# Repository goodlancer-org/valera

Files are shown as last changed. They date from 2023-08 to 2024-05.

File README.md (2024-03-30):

# Valera
Open source hardware and software social robot.






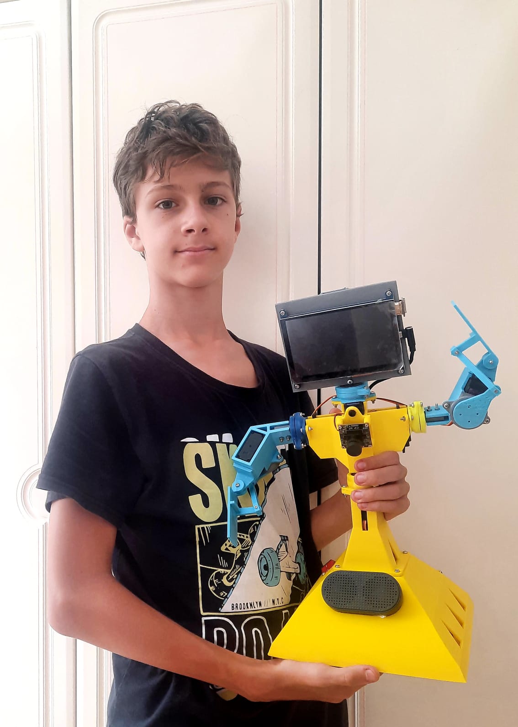
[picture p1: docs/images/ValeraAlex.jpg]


The goal behind the project is to make a social robot with AI on board as cheap and as easy to build and use as it possible.

The project is managed by GoodLancer team.

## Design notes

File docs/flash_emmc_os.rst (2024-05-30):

How to install Linux on eMMC
================================

Before we start
~~~~~~~~~~~~~~~~~

If you don't have a Linux installed on your eMMC you can install one manually.
You will need for this:

#. eMMC card to install Linux to 
#. eMMC-microSD adapter 
#. microSD-USB adapter to plug everything into the PC 
#. Software to flash the eMMC card, i.e. balenaEtcher

Step 1. Download Linux image
~~~~~~~~~~~~~~~

It's better to take an image from the microcomputer manufacturer website, in case of Orange Pi -
from http://www.orangepi.org/html/serviceAndSupport/index.html

3rd party distributions might be more feature rich or performant, but might be leaking some
drivers, i.e. i2c overlays, so in most cases it's safer to stay with Linux distributions 
provided by the microcomputer manufacturer.

In this example we will go with Ubuntu.

Step 2. Flash eMMC with Linux image
~~~~~~~~~~~~~~~

Step 3. Enable i2c in Linux settings
~~~~~~~~~~~~~~~

Use ``sudo orangepi-config`` to enable i2c on the computer how it's 
described on http://www.orangepi.org/orangepiwiki/index.php/Orange_Pi_3B#40pin_I2C_test_2

Step 4. Test if i2c is working
~~~~~~~~~~~~~~~

Check if i2c-2 is switched on by typing ``ls /dev/i2c-*``, you should see i2c-2 device in the list.
Type ``sudo i2cdetect -y 2`` to check if the device is accessible.

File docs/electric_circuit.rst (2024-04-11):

Electric Circuit
==================
On picture below you may see a block scheme depicting how Valera's electric curcuit is composed.
Please note that different versions of the robot uses different microcomputers.
Valera v0.1 utilises microcomputer ODROID-N2L whereas Valera v0.2 utilises Orange PI 3B.
Some images on this page are not updated to the new version of the robot, so if you
see 'Odroid' on the picture - it means any microcomputer, Odroid or Orange PI, otherwise
the difference should be stated in the text.

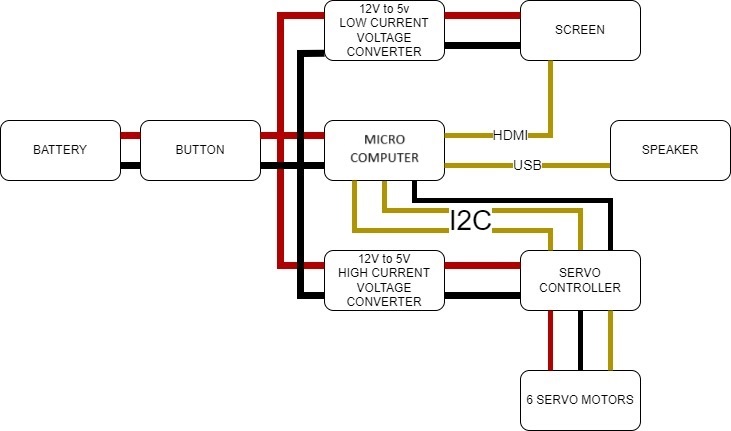
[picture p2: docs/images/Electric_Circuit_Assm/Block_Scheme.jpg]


|

That's how it looks in reality

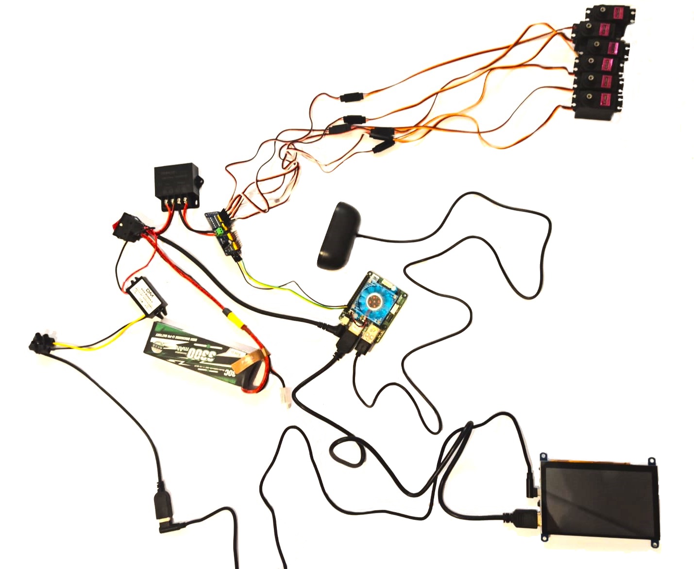
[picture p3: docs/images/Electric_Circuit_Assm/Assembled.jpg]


Assebling Instruction
---------------------

Before we start:
~~~~~~~~~~~~~~~~

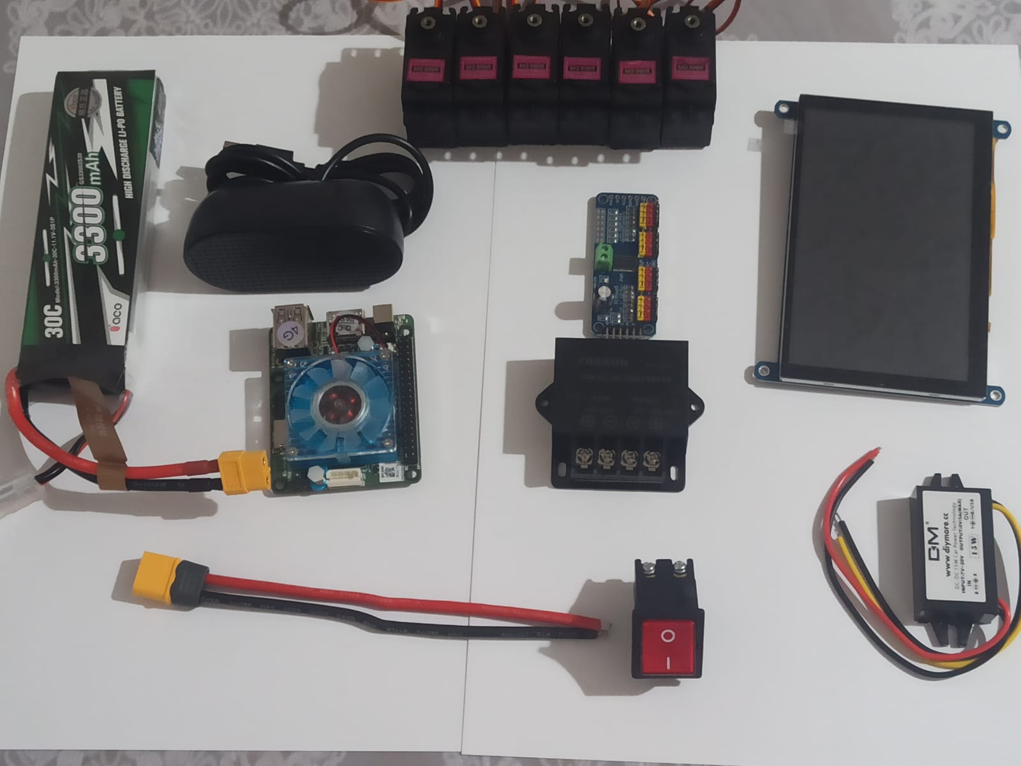
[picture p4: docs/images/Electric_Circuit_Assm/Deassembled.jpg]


Please watch the assembling process video or read a full instruction below.

|

.. raw:: html

    <iframe width="560" height="315" 
    src="https://www.youtube.com/embed/S_Jwx7noY1A?si=5r4jmpi5huq4Ma-H" 
    title="Assembly guide for the electrical circuit of the Valera robot" frameborder="0" 
    allow="accelerometer; autoplay; clipboard-write; encrypted-media; gyroscope; picture-in-picture; web-share" allowfullscreen>
    </iframe>

Step 1
~~~~~~~~~~
Connect low current voltage converter, two wires and jack cable
to the button form one side and XT60 wire from another side. Mind the polarity.

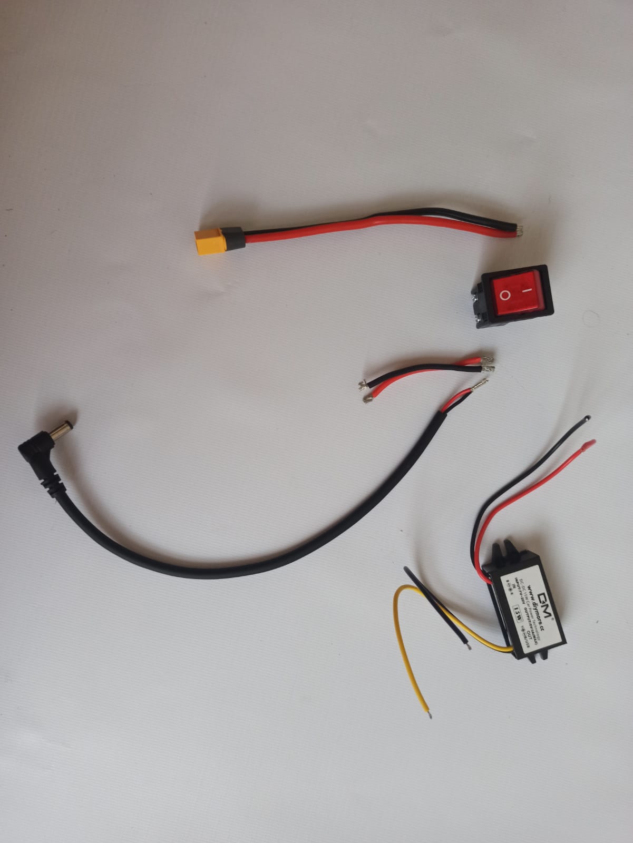
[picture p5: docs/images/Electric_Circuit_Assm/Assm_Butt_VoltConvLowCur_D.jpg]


|

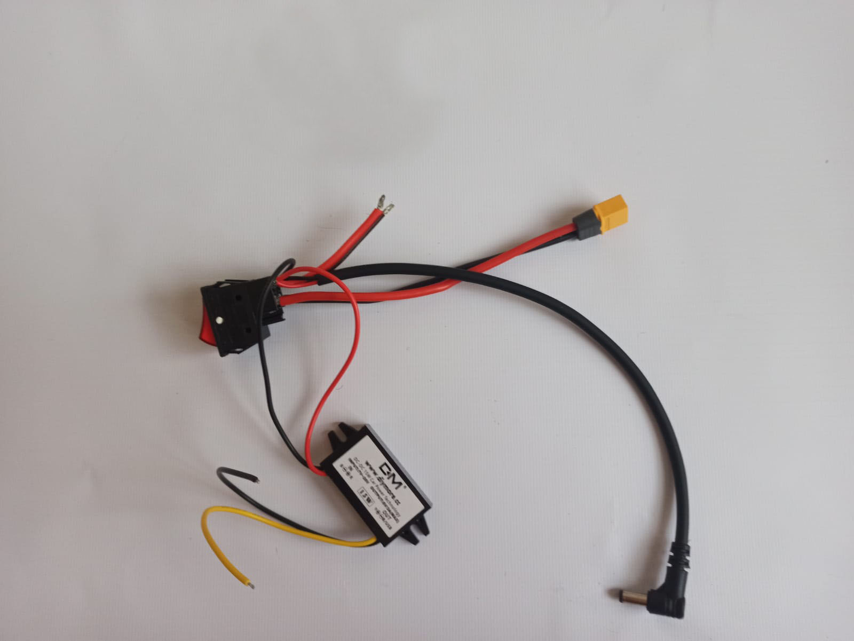
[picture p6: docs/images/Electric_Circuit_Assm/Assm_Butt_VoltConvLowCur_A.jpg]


Step 2
~~~~~~~~~~
Connect an input of the high current voltage converter to the two wires
we connected to the button before. Mind the polarity.

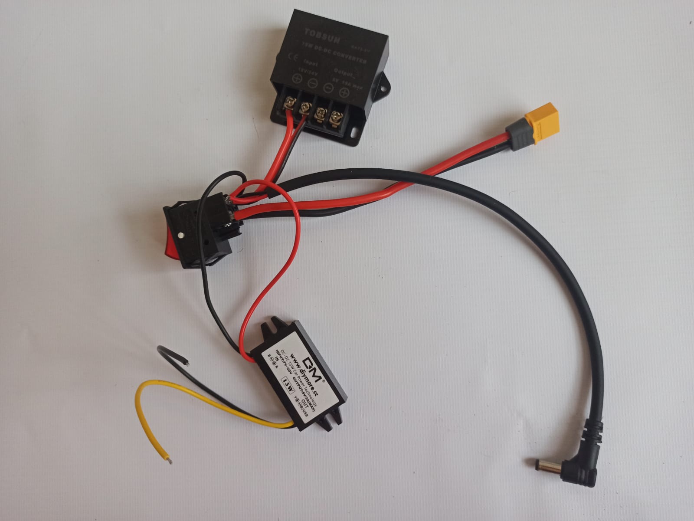
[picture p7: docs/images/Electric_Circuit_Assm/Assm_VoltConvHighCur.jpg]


Step 3
~~~~~~~~~~~
Connect a Servo Controller through two wires to the output of the high current voltage converter. 
Mind the polarity.

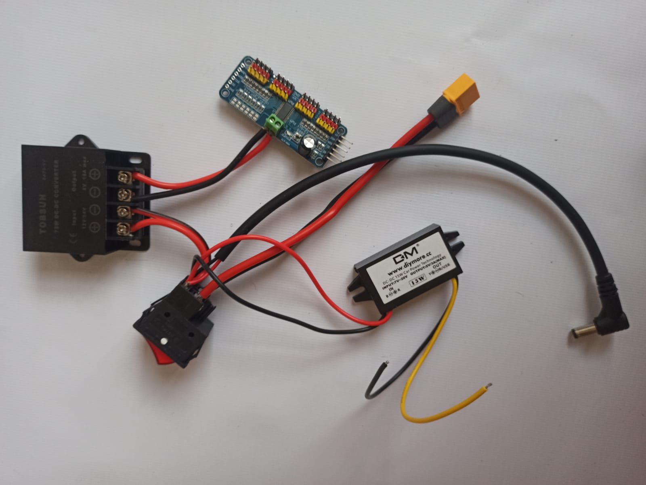
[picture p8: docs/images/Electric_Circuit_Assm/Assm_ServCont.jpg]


Step 4
~~~~~~~~~~~~
Attach the USB wire to the low current voltage converter’s output using screw connectors. 
Pay attention to the polarity.

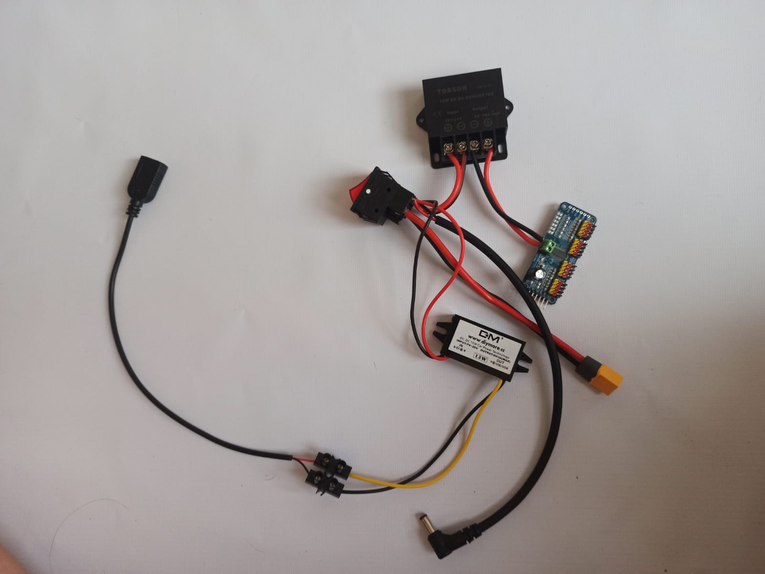
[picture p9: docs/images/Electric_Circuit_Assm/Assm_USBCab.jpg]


Step 5
~~~~~~~~~~~~
Plug in the USB wire to the screen through USB to micro USB L-shaped cable.

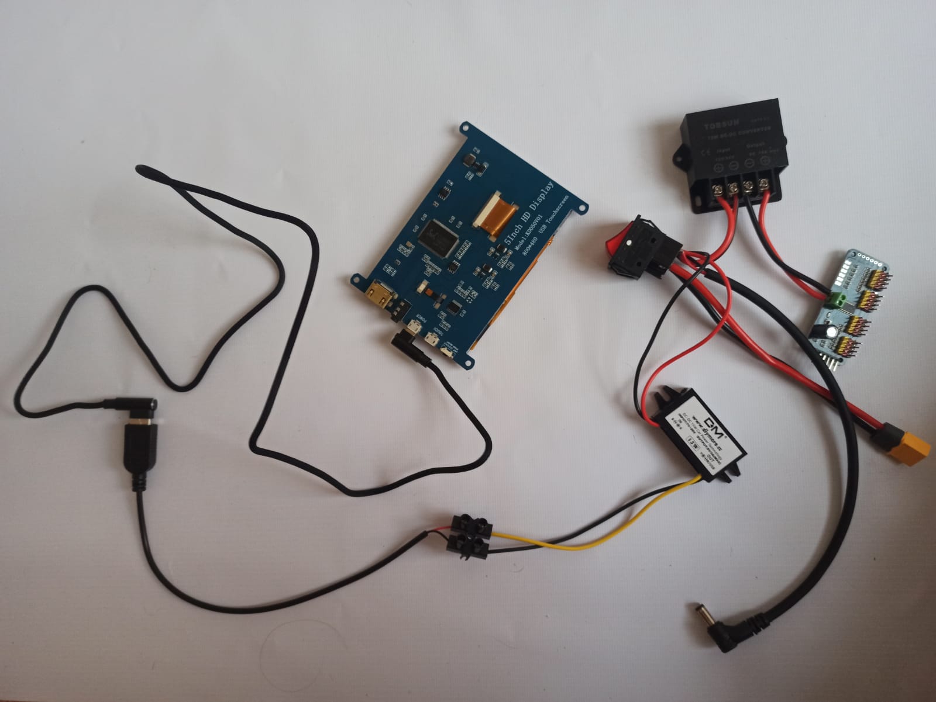
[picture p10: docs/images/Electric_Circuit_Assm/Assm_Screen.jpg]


Step 6
~~~~~~~~~~~~
Plug the jack cable in the microcomputer.

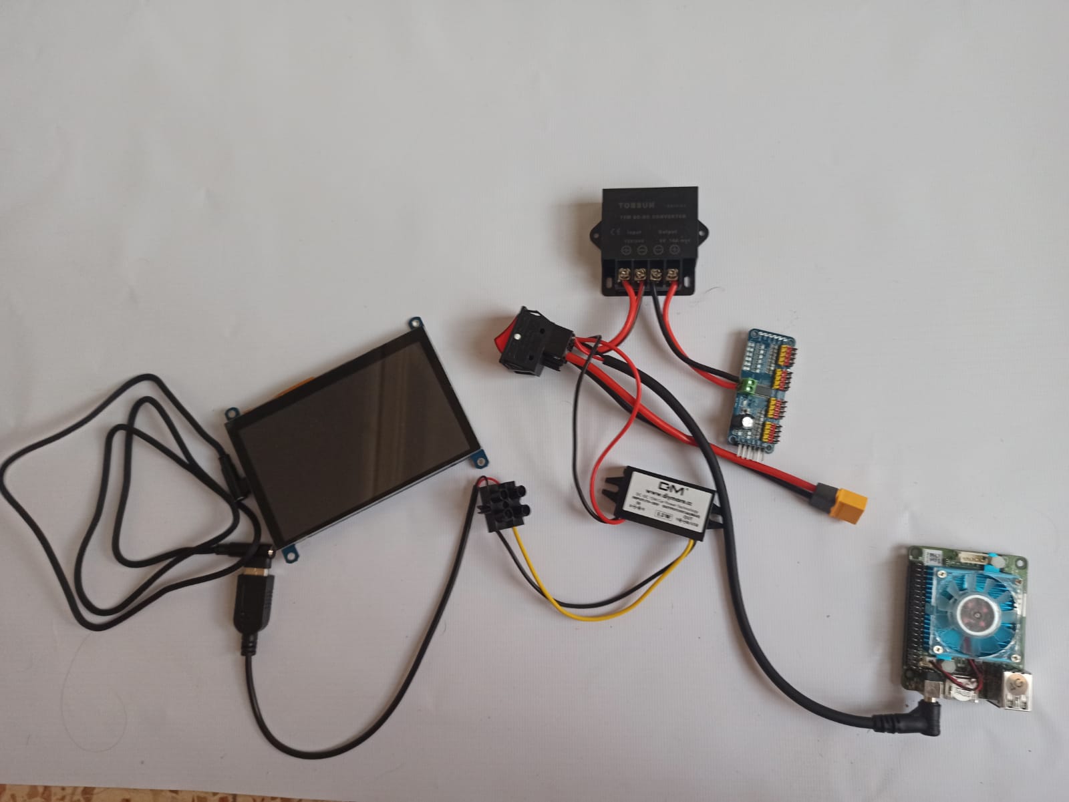
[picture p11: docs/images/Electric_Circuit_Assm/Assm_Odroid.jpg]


Step 7
~~~~~~~~~~~~
Connect the screen to the microcomputer with HDMI cable.

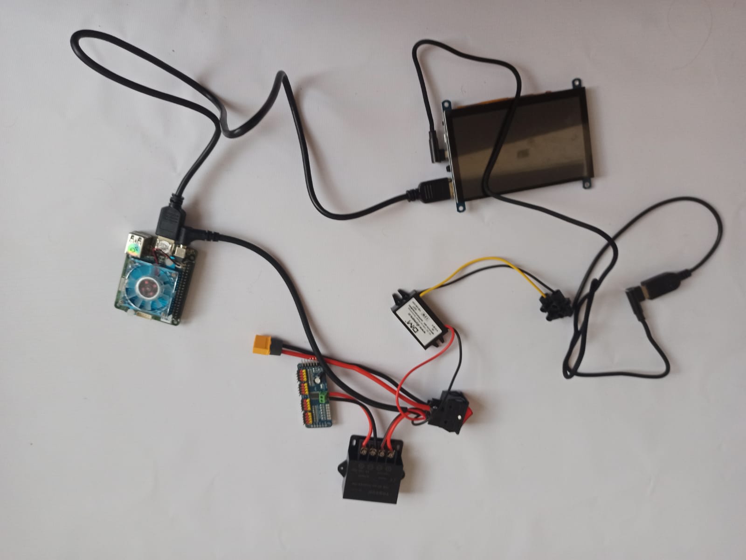
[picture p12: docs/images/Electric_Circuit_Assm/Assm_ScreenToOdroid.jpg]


Step 8
~~~~~~~~~~~
Connect the speaker to the microcomputer using any USB port.

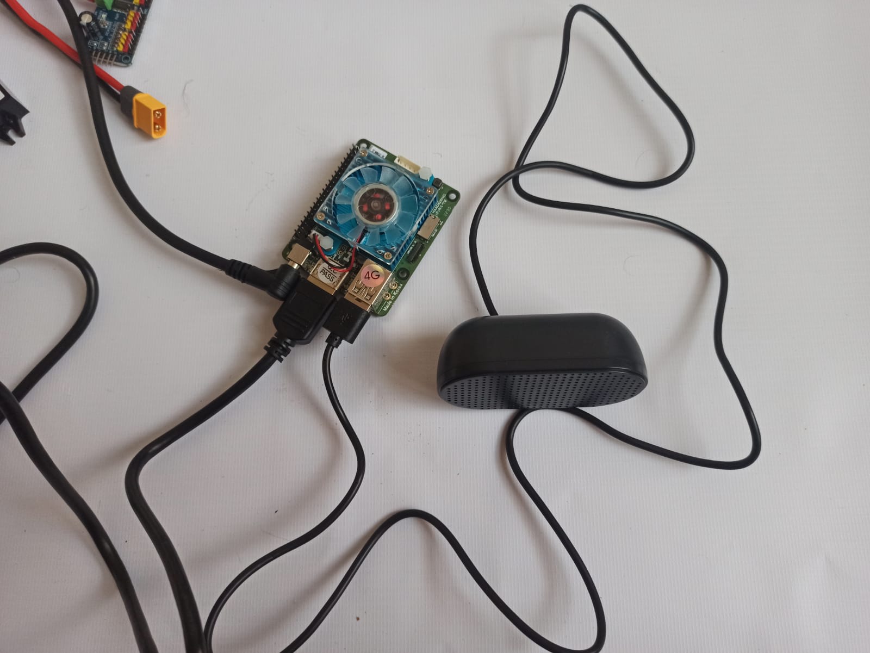
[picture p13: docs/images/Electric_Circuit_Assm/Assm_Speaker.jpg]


Step 9
~~~~~~~~~~~~
Connect the servo controller to the microcomputer using the SCL, SDA, and GND wires. 
The pinout is labeled on the controller. Both microcomputers has the same pinout, please see it below,
but the pin colors differ for different microcomputers:

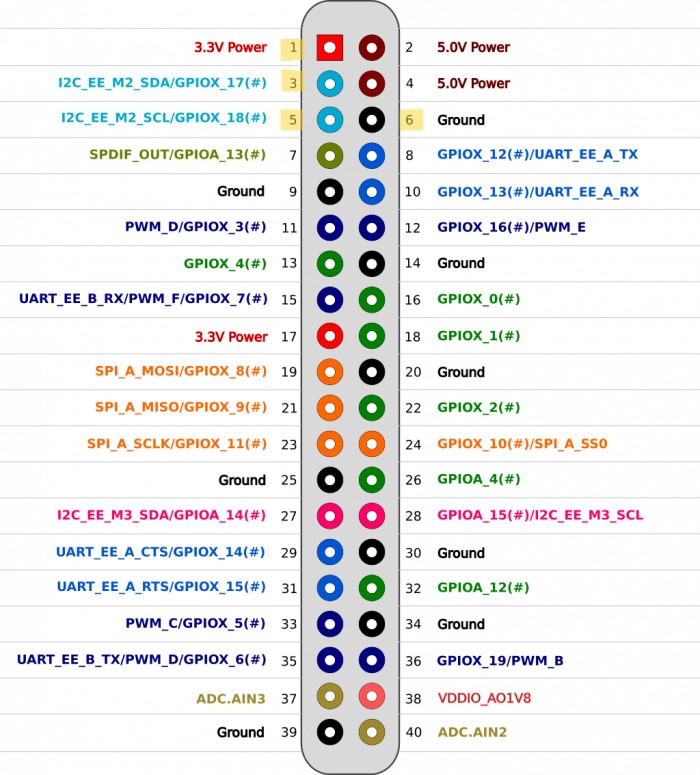
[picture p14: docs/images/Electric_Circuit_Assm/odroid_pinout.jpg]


|

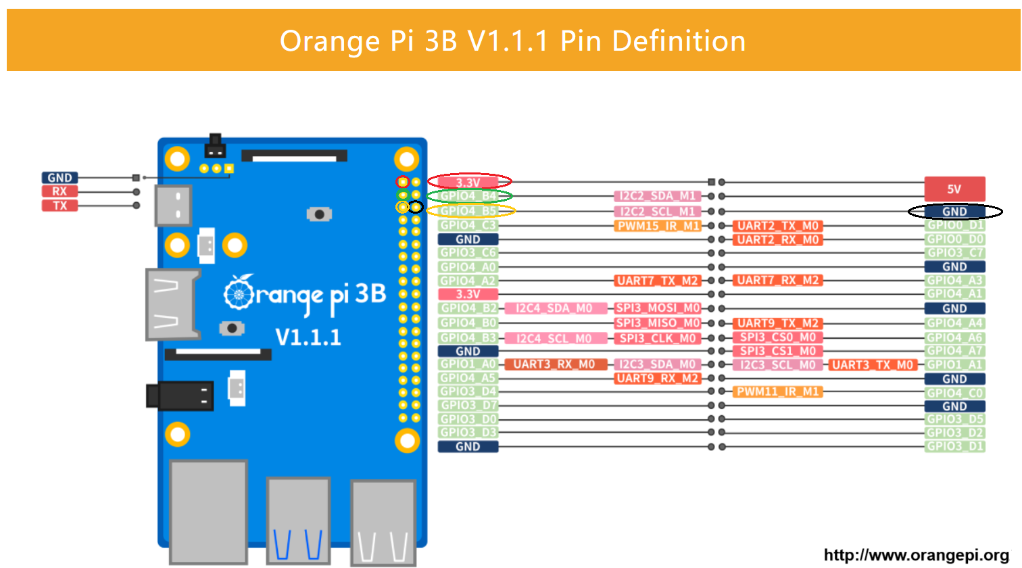
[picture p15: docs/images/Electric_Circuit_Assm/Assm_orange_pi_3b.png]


|

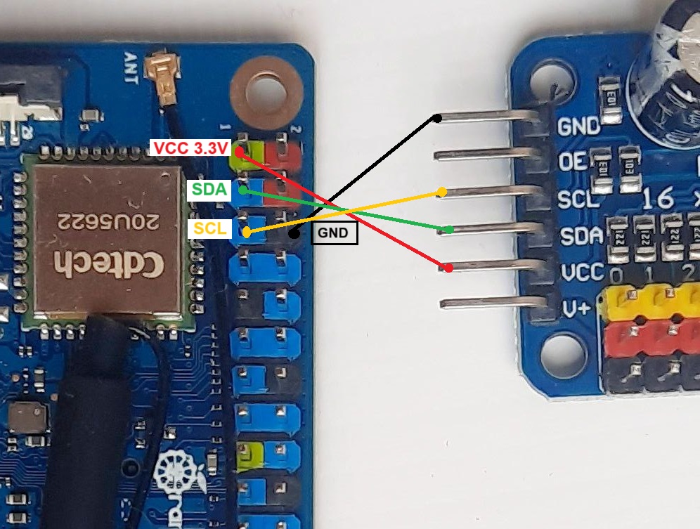
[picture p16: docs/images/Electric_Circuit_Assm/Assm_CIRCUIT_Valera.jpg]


|

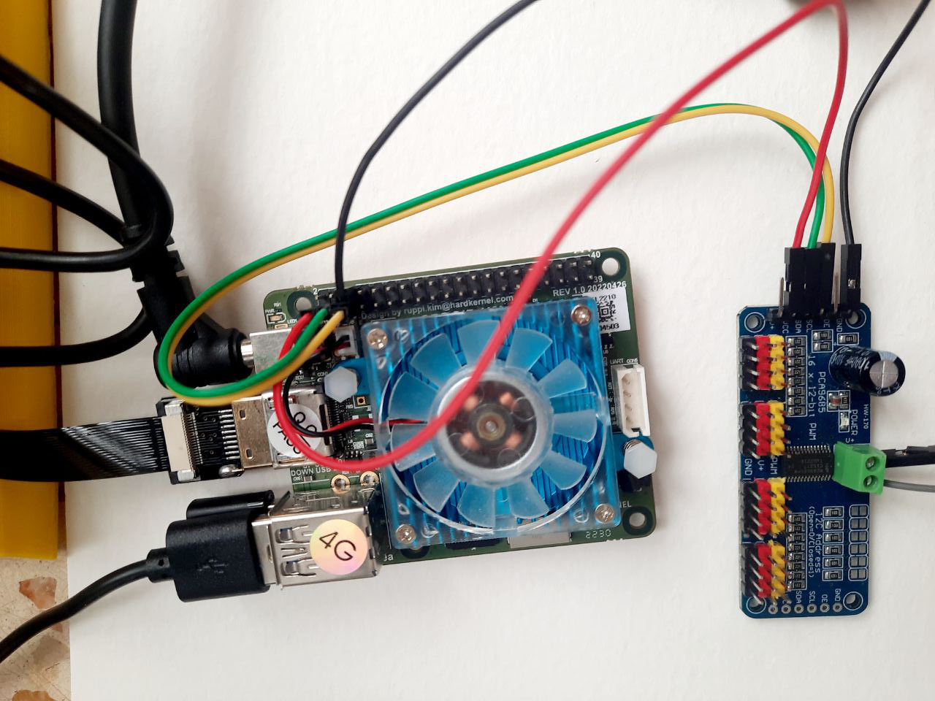
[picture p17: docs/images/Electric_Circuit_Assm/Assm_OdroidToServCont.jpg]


Step 10
~~~~~~~~~~~~
Connect the 6 servos to the servo controller using extension wires. 
Ensure that you connect the data cables to the correct data pins and pay attention to the polarity.
Follow a logical order when connecting the motors to the servo controller. 
For instance, arrange them from top to bottom and left to right. 
The order would be as follows: 

#. Neck
#. Left shoulder
#. Right shoulder
#. Left elbow
#. Right elbow
#. Robot base

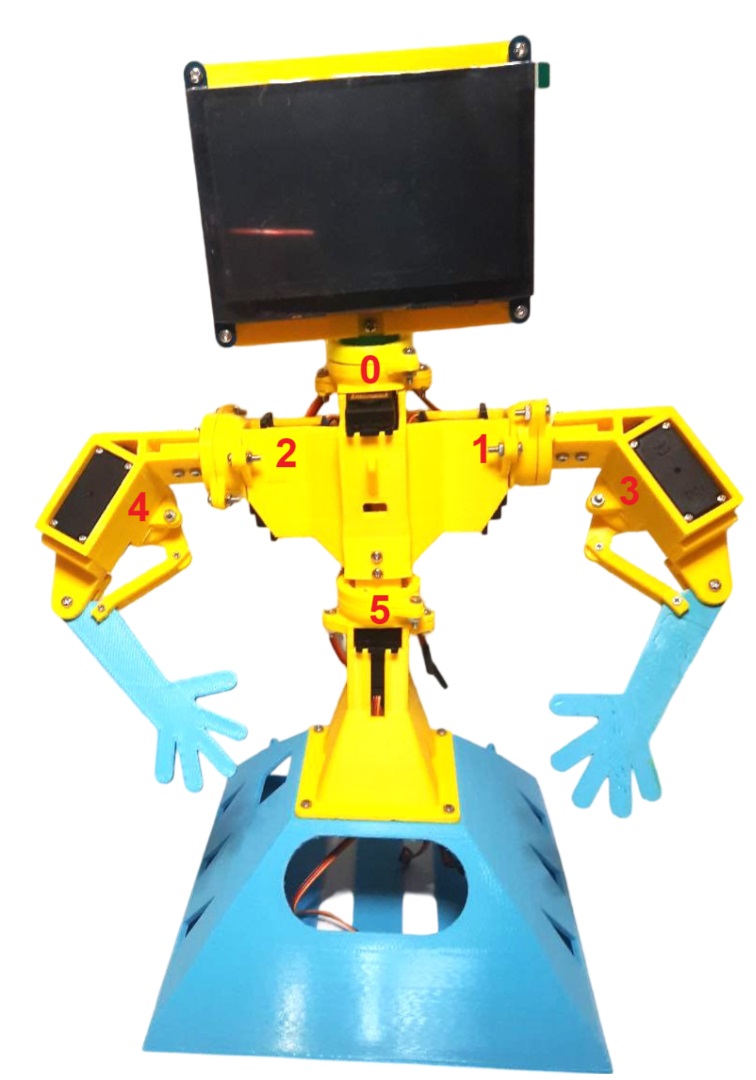
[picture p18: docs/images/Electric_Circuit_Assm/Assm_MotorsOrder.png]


|

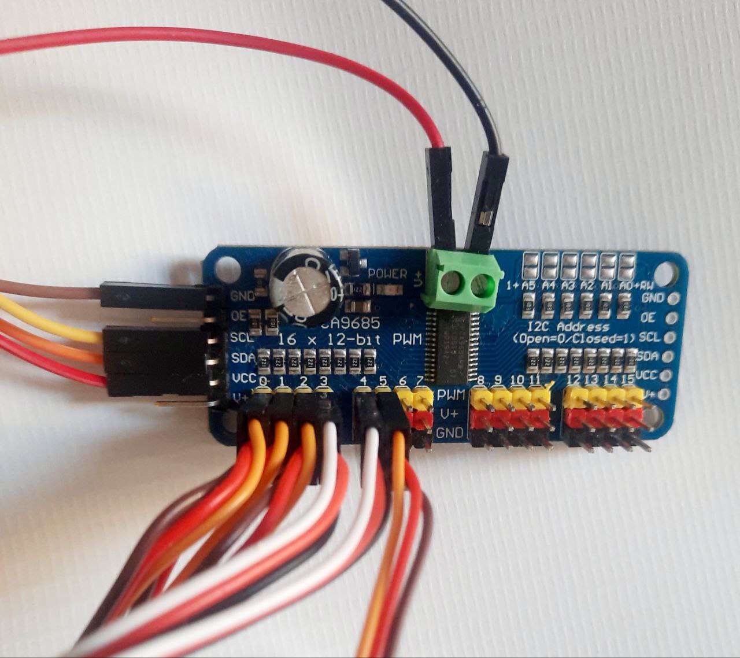
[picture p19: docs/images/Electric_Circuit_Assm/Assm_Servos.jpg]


Step 11
~~~~~~~~~~~~~
Connect the battery to the XT60 wire.

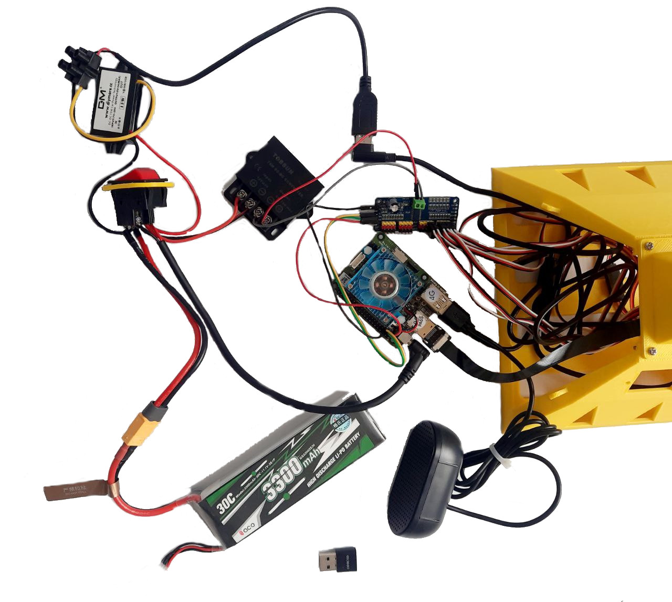
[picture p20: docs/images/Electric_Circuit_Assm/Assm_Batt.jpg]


Finish
~~~~~~~~~~~~~
Congratulations!!! 
Now you can put the assembled scheme into base box and procced to the next step 
in building your own Valera!!!

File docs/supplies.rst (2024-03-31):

Supplies
========

Components for the robot are widely used and can be bought in different places.
We don't recommend any suppliers mentioned via links below - please select any shops/suppliers you like,
the links are provided only for reference.

* Single-board computer like Raspberry PI, Odroid or Orange PI as a braind with AI, camera and sound sensors
* 3d-printing with regular PLA
* Cost-effective servo motors and electronics

The robot can be also ordered as a kit (electronics only, electronics + 3d-printed parts, or fully assembled robot) from us.
To make an order please contact us via `Goodlancer order form <https://forms.gle/yLRHZK9KKtq2HRJS9>`_ .

List of components
------------------

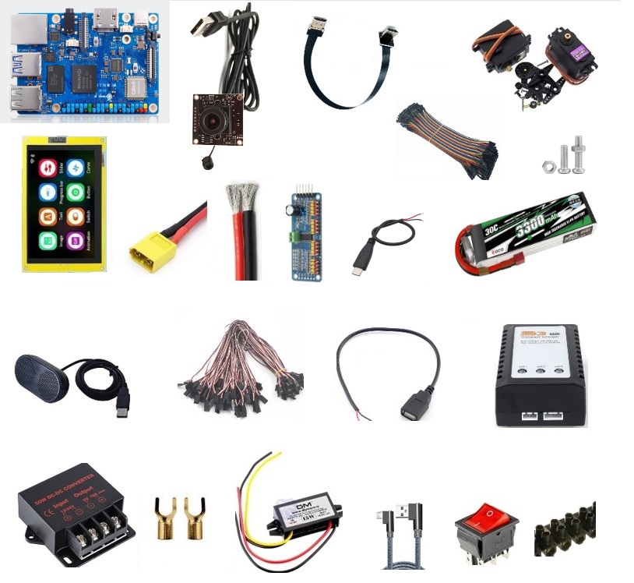
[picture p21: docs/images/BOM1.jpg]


|

#. Microcomputer - select one version
    * Version 0.1 - with Odroid-N2L, 4Gb RAM, 32Gb eMMC
        #. `ODROID-N2L with 4GByte RAM <https://www.hardkernel.com/shop/odroid-n2l-with-4gbyte-ram/>`_ $69 
        #. `WiFi Module 5BK <https://www.hardkernel.com/shop/wifi-module-5bk/>`_ $8.9
        #. `12V/2A power supply Asia/Korea round plug <https://www.hardkernel.com/shop/12v-2a-power-supply-asia-korea-round-plug/>`_ $5.5
        #. `16GB eMMC Module N2L Linux <https://www.hardkernel.com/shop/16gb-emmc-module-n2l-linux/>`_ $13
        #. `DC Plug Cable Assembly 5.5mm L Type <https://www.hardkernel.com/shop/dc-plug-cable-assembly-5-5mm-l-type/>`_ $1.3
    * Version 0.2 - with Orange PI 3B, 8Gb RAM, 256Gb eMMC
        #. `Orange PI 3B 8Gb with eMMC <https://www.orangepi.org/html/hardWare/computerAndMicrocontrollers/details/Orange-Pi-3B/>`_ $80
#. `Camera Module 3.6mm with Microphone NEO Coolcam 30fps HD 4MP 2560x1440 USB <https://a.aliexpress.com/_EGyLnnt>`_ $20
#. `Adafruit PCA9685 Servo controller <https://www.aliexpress.com/item/32466332558.html>`_ $4
#. `screws m2,m3 , nuts <https://www.aliexpress.com/item/32801531985.html>`_ $10
#. `MG996R Servo 6 pieces <https://www.aliexpress.com/item/4000417528570.html>`_ $45
#. `PLA (1kg) base and details <https://a.aliexpress.com/_mrTfJzM>`_ $50
#. `Servo tester <https://a.aliexpress.com/_mLtn8Ea>`_ $7 used for motor testing
#. `LiPo battery Gens ACE 3300mAh 3S XT60 <https://www.aliexpress.com/item/1005003720800196.html>`_ $37.9
#. `Power wires XT60 female <https://www.aliexpress.com/item/1005005297368178.html>`_ $6
#. `20 AWG 2pins wire <https://www.aliexpress.com/item/1005001876813940.html>`_ $3.7
#. `ESP-LCD Display 800*480 ips rgb,8M PSRAM,16M flash <https://www.aliexpress.com/item/1005004788147691.html>`_ $28.1
#. `Speaker hk-5002 <https://a.aliexpress.com/_EwVoRaH>`_ $13.5
#. `Servo extension wires 300mm FM <https://www.aliexpress.com/item/4001293611208.html>`_ $0.3 
#. `Display power wires 2pin usb-B <https://www.aliexpress.com/item/1005005005072094.html>`_ $1.6
#. `LiPo Charger 3S XT-60 <https://www.aliexpress.com/item/1005003986195734.html>`_ $7.6
#. `DC power converter 12V to 5V 15A for motors <https://www.aliexpress.com/item/1005003324739838.html>`_ $10
#. `DC power converter 12V to 5V 3A for display <https://www.aliexpress.com/item/33011470040.html>`_ $3
#. `Micro USB Typec Cable L-shape 1м <https://www.aliexpress.com/item/1005003132076690.html>`_ $2
#. `Micro USB Female 2P Charger Wire Connector <https://www.aliexpress.com/item/1005005904505797.html>`_ $2
#. `Micro USB Type c Cable 2 pin for Orange Pi <https://a.aliexpress.com/_oEXXAG4>`_ $7.7
#. `Rocker Switch With Light 4 Screw  <https://www.aliexpress.com/item/1005003597120974.html>`_ $1
#. `Crimp Spade Terminal connector pack <https://www.aliexpress.com/item/1005003611683326.html>`_ $10.6
#. `Jumper wire dupont cable for DIY kit female to female and male to male (red and black) <https://www.aliexpress.com/item/4000203371860.html>`_ $0.5
#. `HDMI L-shaped wires A1-A2 50cm <https://www.aliexpress.com/item/1005002200767476.html>`_ $5
#. `Screw terminal 12-pole 10A <https://www.aliexpress.com/item/1005002760392481.html>`_ $1

TOTAL PRICE ESTIMATION : $400
** Prices are approximate and may vary, they do not include shipping costs and customs duties.

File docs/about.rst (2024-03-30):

About Valera and social robots
=========================



Valera is a social robot aimed to be the cheapest one able to communicate with people and emotionally react to them.
Valera can act as a friend or a teacher. 

.. note::
  The Valera 0.2 release offers significant improvements over its predecessor. 
  With 8GB of RAM (compared to 4GB in version 0.1) and 256GB of permanent storage 
  (up from 16GB or 32GB), it provides enhanced performance and capacity. 
  Additionally, Valera 0.2 introduces new software features, including AI models, 
  ROS2, and devcontainer integration. While we’re in the process of updating the documentation, 
  please note that most of the existing documentation for version 0.1 can still be applied 
  to the current version, although it may not cover all the new possibilities.

What are social robots
--------------------------------

Social robots can keep human knowledge and culture the same way as do books, photos, movies, 
stories and so on. Even if there only one person left in the world holding some rare culture, 
social robots can learn this culture and spread it. They cannot replace real persons, 
but they can be made in big quantities, they never forget, never are too busy, too old or sick.

Social robots can listen, understand feelings, react. They can teach and they can be tought.

This is how we see social robots.

What (or who) is Valera 
--------------------------------

Valera is extremely easy and cheap to build and customize.
We provide all the documentation for both the robot hardware and software free of charge.

Valera born to be a social robot, but currently he is not ready to function as one, he is a work in process
and at the current stage we use Valera as an example to describe how to build cost effective robots with
AI and modern software on board easily.

Technologies and components used
--------------------------------

* Single-board computer like Raspberry PI or Odroid as a braind with AI, camera and sound sensors
* 3d-printing with regular PLA
* Cost-effective servo motors and electronics

Get the files
-------------

The files - 3d source, STL files for 3d-printing and code for the robot is available on `Github <https://github.com/goodlancer-org/valera>`_ . 
Electronics components can be bought anywere, please see :doc:`supplies`.

License
-------

Valera (both software and hardware) is licensed under the MIT license. 
This means that you are free to modify, distribute and republish the source code 
on the condition that the copyright notices are left intact. 
You are also free to incorporate Valera into any Commercial or closed source application.

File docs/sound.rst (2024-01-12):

How to setup and process sounds
================================

Before we start
~~~~~~~~~~~~~~~~~

The robot uses an external USB speaker to play sounds. Please ensure that the speaker is connected to the microcomputer.

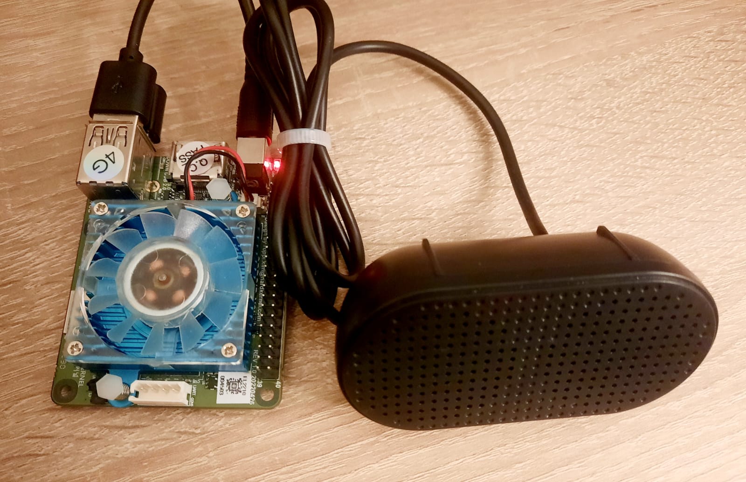
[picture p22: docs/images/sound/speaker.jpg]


Step 1. Power up Odroid
~~~~~~~~~~~~~~~

Ensure that a WiFi dongle and a speaker are inserted into the Odroid's USB ports, 
and that the WiFi connection is configured for the microcomputer. 
Power up the Odroid and establish a connection to it using MobaXTerm.

Step 2. Setup sound level
~~~~~~~~~~~~~~~

Enter ``alsamixer`` in the terminal to open the audio volume configuration utility.

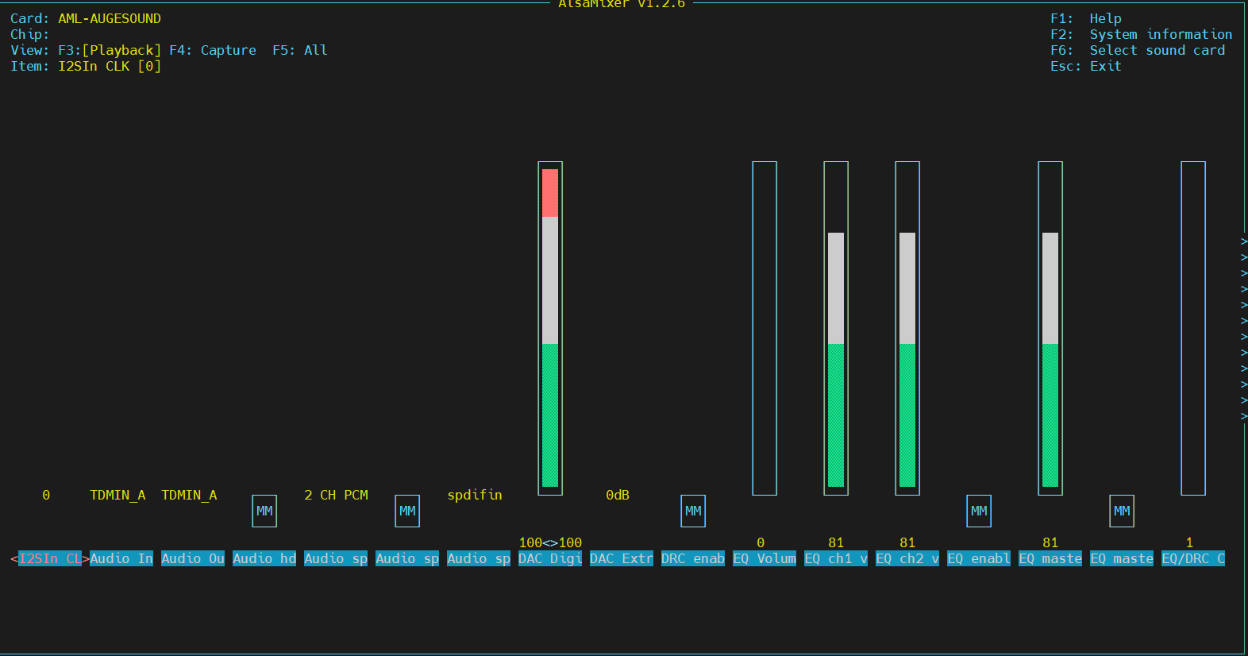
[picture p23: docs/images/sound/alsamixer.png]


Press ``F6`` and select UACDemoV1.0 sound card. 

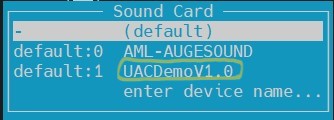
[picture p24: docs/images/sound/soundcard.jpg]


The initial sound level may be set to 20%. It can be increased to 100% using the button ``↑``

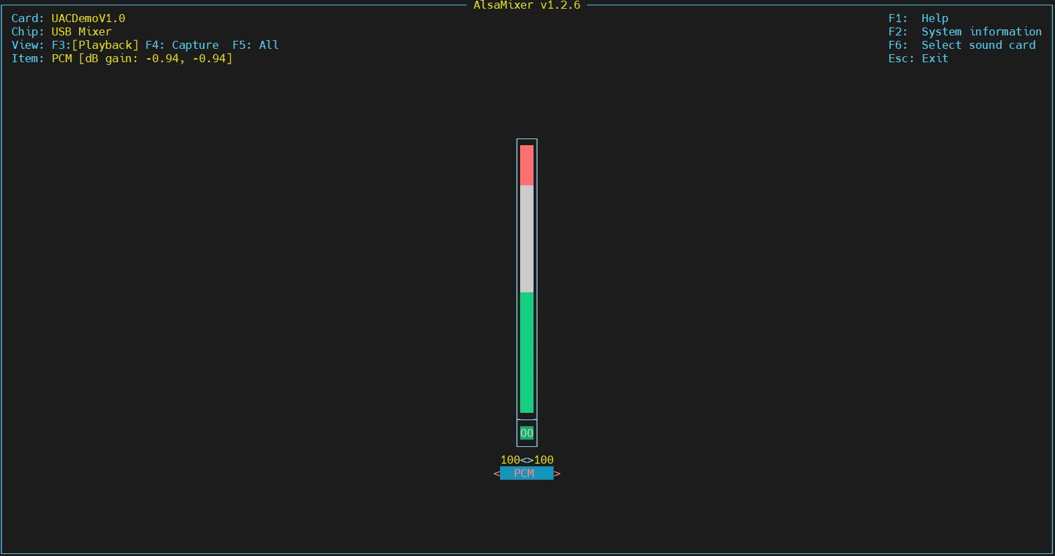
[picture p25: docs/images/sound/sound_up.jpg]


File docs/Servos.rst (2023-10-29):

Servo motors
==================

Servo motors drive Valera and this is essential to set the up and test like it's show on the video below.

.. raw:: html

    <iframe width="560" height="315" 
    src="https://www.youtube.com/embed/7wUNU5IKYxU?si=-xs0XWdKWBbhhZVB" 
    title="Valera robot YouTube video" frameborder="0" 
    allow="accelerometer; autoplay; clipboard-write; encrypted-media; gyroscope; picture-in-picture; web-share" allowfullscreen>
    </iframe>

|

A servo motor is a motor equipped with an integrated movement sensor, 
typically a simple potentiometer, which allows for the control of the motor's rotation angle. 
Here's the schematic diagram:



    Servo Scheme

There are two types of servo motors: angle-controlled and speed-controlled. 
Here we focus solely on the angle-controlled ones.

Angle servos are commonly referred to as 180-degree servos, but in reality, 
their range may vary and is not always exactly 180 degrees. 
It can be around 120, 270, or even 360 degrees, depending on the specific servo you purchase. 
In our case, it's approximately 120 degrees, 
so you must always be mindful of the position when installing a servo in your project 
to maximize its potential.

Servos are operated by sending them serial pulses, 
where the width of the pulse instructs the motor on which angle to turn.



    Servo Signal

For testing or manually adjusting servos when necessary, we use a servo tester device. 
This device allows you to connect and control several motors simultaneously, 
which is particularly useful for checking the angle range of your motors or verifying the accuracy 
of your assembly.



    Servo Tester

When you need to control your servos automatically, you use a servo controller. 
It's a compact circuit board that typically receives PWM signals, 
although there may be variations, 
so it's essential to consult your controller's documentation for specific details.



    Servo Controller

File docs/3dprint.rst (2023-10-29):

Printing the parts
=========================

Facilities
--------------------

Every 3D printer can be used, the only requirement is to have a table not smaller than 20cmx20cm, because it's the size of our biggest part.
Also every type of filament can be used, we have used PLA.
No special knowledge is need, if you know the very basics of 3d printing, you can print the project.



All time assumptions are made for printer Prusa Mk4 with 0.4mm nozzle with 20% unless otherwise said.

Parts
---------------------



    The robot assembly 

The robot body consists of 4 main blocks:

* 1 - Base (red)
* 2 - Chest (green)
* 3 - Head (blue)
* 4 - Arms (yellow)

.. raw:: html

    <div class="sketchfab-embed-wrapper"> 
    <iframe title="Social robot Valera (assembly)" frameborder="0" allowfullscreen mozallowfullscreen="true" webkitallowfullscreen="true" allow="autoplay; fullscreen; xr-spatial-tracking" xr-spatial-tracking execution-while-out-of-viewport execution-while-not-rendered web-share width="640" height="480" src="https://sketchfab.com/models/b62bbd69dae34dabb491808437f7caf9/embed?autostart=1"> 
    </iframe> <p style="font-size: 13px; font-weight: normal; margin: 5px; color: #4A4A4A;"> 
    <a href="https://sketchfab.com/3d-models/social-robot-valera-assembly-b62bbd69dae34dabb491808437f7caf9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" target="_blank" rel="nofollow" style="font-weight: bold; color: #1CAAD9;"> 
    Social robot Valera (assembly) </a> by 
    <a href="https://sketchfab.com/goodlancer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" target="_blank" rel="nofollow" style="font-weight: bold; color: #1CAAD9;"> 
    GoodLancer </a></p></div>

|

Total weight of filament needed for all the parts is about 680 g .
Total printing time on a fast rate will be around 24 hours .

Both STL files to print and source models for FreeCAD can be found 
on `Github <https://github.com/goodlancer-org/valera>`_ in `STL` and `3d source` folder
respectively.

1 - Base
--------------------------------



    Base assembly

* 1_Base_Box - 270 g printing time 9 h
* 1_Base_Stand - 55 g printing time 1 h
* 1_Base_Door - 25 g printing time 2 h
* 1_Base_Switch - 3 g printing time 8 mins

Total weight of the Base parts is 353 g and total time is 12 hours.



    Base parts

2 - Chest
--------------------------------



    Chest assembly

* 2_Chest_Main - 77 g printing time 3 h 
* 2_Chest_joint_Big - 8 g printing time 20 mins
* 2_Chest_joint_Small - 7 g printing time 20 mins X2
* 2_Chest_joint_Cap -  3 g printing time 8 mins X3
* 2_Chest_Motor_Cap - 7 g printing time 17 mins X4
* 2_Chest_Camera_Mount - 6 g printing time 18mins

Total weight of the Chest parts is 129 g and total printing time is 5 hours 30 minutes



    Chest parts

3 - Head
--------------------------------



    Head assembly

* 3_Head_Main - 65 g printing time 1 h 23 mins
* 3_Head_Mount - 8 g printing time 14 mins

Total weight of the Head parts is 73 g and total printing time is 1 hours 40 minutes



    Head parts

4 - Arm 
--------------------------------



    Arm assembly

* 4_Arms_Rod - 3 g printing time 10 mins X2
* 4_Arms_Lever_R - 7 g printing time 12 mins
* 4_Arms_Lever_L - 7 g printing time 12 mins
* 4_Arms_Bracket_R - 8 g printing time 19 mins
* 4_Arms_Bracket_L - 8 g printing time 19 mins
* 4_Arms_Main_R - 26 g printing time 52 mins
* 4_Arms_Main_L - 26 g printing time 52 mins
* 4_Arms_Cap - 6 g printing time 15 mins X2
* 4_Arms_Palm - 10 g printing time 24 mins X2

Palm and Rod have to be printed with 100% filling.

Total weight of the two Arms parts is 123 g and total printing time is 4 hours 25 minutes



    Arm parts

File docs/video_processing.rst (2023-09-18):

How to process robot video
================================

Before we start
~~~~~~~~~~~~~~~~~

The robot utilizes USB camera to explore the environment.

To get started with video processing you will need the following:

* single board computer Odroid with WiFi and SSH set and running
* USB WiFi dongle
* Odroid power cable
* USB web camera
* SSH terminal client software installed on PC or laptop. We'll be using MobaXTerm for
demonstration purposes, but any other SSH terminal client can be used.

Insert WiFi dongle and web camera into Odroid's USB ports and you're ready to go.

Step 1. Power up Odroid
~~~~~~~~~~~~~~~

Ensure that WiFi dongle and web camera are inserted into the Odroid's USB ports and
WiFi connection is set for the microcomputer. Power up Odroid and connect to it
with MobaXTerm.

Step 2. Copy Valera code to Odroid 
~~~~~~~~~~~~~~~

Valera code is a free and open source software repository with example code to control the robot.
Create a separete folder to store the code: ``mkdir Code && cd Code``

Copy the repository code to the new folder: ``git clone https://github.com/goodlancer-org/valera-code``
Change the current working directory to the folder with code: ``cd valera-code``

Step 3. Run Valera code 
~~~~~~~~~~~~~~~

Valera code includes files to run docker, to start a JupyterLab server on Odroid and workbooks
with example code for the robot.

To start Valera code type ``sudo docker compose up``

When the server is running go to your laptop, open a browser and navigate to
``http://[odroid_ip_address]``, in my case it will be ``http://192.168.1.226``

The password for Jupyter is ``Valera``



Step 4. Explore and run example code 
~~~~~~~~~~~~~~~

When in Jupyter open up 'work' folder to see the example workbook.



Double click ``video.ipynb`` file to open example code.



Run example code to see how the camera works:

.. raw:: html

   <video width="100%" controls src="_static/jupyter_video.mp4" type="video/mp4" autoplay>
   camera video embedded in Jupyter notebook
   </video>

The simpliest code to read images from the camera is as follows:

.. code-block:: python

   # Activate camera object
   cap = cv2.VideoCapture(0)

   # Take a picture
   _, frame = cap.read()

   # Convert the picture to bytes
   _, frame = cv2.imencode('.png', frame)
   frame = frame.tobytes()

   # Release the camera object
   cap.release()

Finish
~~~~~~~~~~~~~~~~~~~

All the example code for Valera (dockerfiles, docker compose, shell scripts, python code)
is provided free and open source. Please feel free to change it to adopt to your needs.

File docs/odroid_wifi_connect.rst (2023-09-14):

How to connect your odroid to wifi
================================

Before we start
~~~~~~~~~~~~~~~~~

You will need the following:

* single board computer Odroid
* USB keyboard
* HDMI cable
* display or TV with HDMI input
* Odroid power cable

Then you need to assmeble this primitive electric sheme:
Connect a keyboard to you Odroid, connect your Odroid to the display with hdmi cable and plug the odroid to a socket using a power cable



Step 1. Log into odroid
~~~~~~~~~~~~~~~

Now log into your odrdoid as a user, NOT as a guest



Step 2. Open terminal
~~~~~~~~~~~~~~~~~~~

Open terminal using combination of keys ``Ctrl+Alt+T``. Use ``F10`` to make it full screen if needed.



Step 3. Check linux version
~~~~~~~~~~~~~~~~~~~~~~

Type ``lsb_release -a`` to check your linux version. It should be ubuntu 22.04



Step 4. Check wifi status and interface
~~~~~~~~~~~~~~~~~~

Now type ``nmcli dev status`` to check WiFi status, it should be disconnected.
Aslo check your interface type, you'll need it further. For me it's wlan0



Step 5. Check the list of available networks
~~~~~~~~~~~~~~~

Type ``iwlist wlan0 scan | grep ESSID`` to check the list of available wifi networks. 
If your interface is different from wlan0 use ``iwlist scan <your interface> scan | grep ESSID``



Step 6. Connect to Wifi
~~~~~~~~~~~~~~~~~~~~

Type ``sudo nmcli dev wifi connect <your network name> password <your network password>``
Then odroid will ask for user's password, for odroid board the default one is ``odroid``



Step 7. Check if everything connected correctly
~~~~~~~~~~~~~~~~~~~~

Now you can again type ``nmcli dev status`` to make sure you cennected successfully,
it should say "connected" and display correct network name.



Step 8. Check internet connection
~~~~~~~~~~~~~~~~~~~~

Type ``ping -c 5 8.8.8.8`` to see if the computer is connected to the Internet. 8.8.8.8 is a Google server.



Step 9. Know your IP address
~~~~~~~~~~~~~~~~~~~~

Now that you have your Odroid connected to WiFi it can be accesses and managed from any 'normal' computer
using ssh. SSH server should be running on the Odroid (and it is by default), so to get connected
to Odroid one need to know:

* login - odroid 
* password - odroid 
* IP address, which we can find by typing ``hostname -I``.



In this case on the picture the IP address is 192.168.1.226

Step 10. Connect to Odroid with external terminal
~~~~~~~~~~~~~~~~~~~~

Now that you have your Odroid connected to WiFi it can be accesses and managed from any 'normal' computer
using ssh. SSH server is already installed and running on Odroid, so let's install ssh client software
onto Windows computer and connect it to the Odroid.

Any SSH client can be used, the one we prefer is MobaXterm Home Edition (free) 
- https://mobaxterm.mobatek.net/download.html

Download it, install and setup ssh session as it's shown on a picture below:



Double click session name and try to connect to the Odroid:



Finish
~~~~~~~~~~~~~~~~~~~

Congratulations!!! If all the steps are performed correctly now you don't need to connect your
Odroid device to the display or keyboard to be able to manage it. On power up the microcomputer
will be connecting to the WiFi network and can be managed from any 'normal' computer in the same
WiFi network and with ssh client software installed.

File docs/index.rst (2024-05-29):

Welcome to social robots' world!
===============================================

Valera is a social robot, which means that the goal is to make robot to be a part of a society, 
keep some human knowledge and human culture, to be able to learn and analyse,
to be able to communicate like people do and to share.

The second goal was to make the robot cheap, affordable and easy to build, even by kids and at home.



.. toctree::
   :maxdepth: 2
   :caption: 👱 About
   :hidden:

   about

.. toctree::
   :maxdepth: 2
   :caption: 🚀 How to build
   :hidden:

   supplies
   3dprint
   electric_circuit

.. toctree::
   :maxdepth: 2
   :caption: 🖳 Software installation
   :hidden:
   
   flash_emmc_os
   odroid_wifi_connect
   docker_and_jupyter
   video_processing
   servos
   sound

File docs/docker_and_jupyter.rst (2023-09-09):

Launch a web server on Odroid
================================

We install a container management system, docker, onto Odroid to run any software
from image files with no need to install anything else to the microcomputer but
the docker. Finally we'll test the docker by running a web server with popular
interactive development environment (IDE) - jupyterlab.

Web server running on Ordoid provides access to the microcomputer
from any device in the same WiFi network, i.e. from laptop.

Before we start
~~~~~~~~~~~~~~~~~

To install docker we have to have:

* single board computer Odroid with WiFi and SSH set and running
* Odroid power cable
* SSH terminal client software installed on PC or laptop. We'll be using MobaXTerm for
demonstration purposes, but any other SSH terminal client can be used.

Step 1. Power up Odroid
~~~~~~~~~~~~~~~

Ensure that WiFi donglo is inserted into an Odroid USB port and
WiFi connection is set for the microcomputer. Power up Odroid and connect to it
with MobaXTerm.





Step 2. Install docker on Odroid
~~~~~~~~~~~~~~~~~~~

Now we can manage Odroid from MobaXTerm window as it we were working directly on
the microcomputer over command line terminal.

Let's update the system first:

``sudo apt-get update && sudo apt-get upgrade``

``sudo apt install ca-certificates curl gnupg lsb-release``

Install docker itself using the official installation script:

``sudo curl -sSL https://get.docker.com | sh``

Step 3. Check if the docker is working
~~~~~~~~~~~~~~~~~~~

First, let's check if the docker installed using ``sudo docker version`` or ``sudo docker info``

If everything is ok the version info appears:



Now check if the docker is running by typing ``sudo systemctl status docker``:



Next, let's try running a simple container:

``sudo docker run hello-world``



If you're using a stock Odroid linux image you might encounter a problem with permissions
to use docker which look like one on the next picture: 



If you see this error perform the action shown on the next stem and try running
hello-world docker container again.

Step 4. Fix cgroup error
~~~~~~~~~~~~~~~~~~~

To do so we'll need to add a line of code in the boot file.

Run ``sudo nano /media/boot/boot.ini`` and add a line 
``setenv bootargs "${bootargs} systemd.unified_cgroup_hierarchy=0"``
as it shown on picture below:



Now try running ``sudo docker run hello-world`` again and everything should be working.

Step 5. Run JupyterLab
~~~~~~~~~~~~~~~~~~~

JupyterLab is a popular IDE for data scientists and not only for them.
We can run it on our Odroid in docker and access is from any computer in the same
WiFi network.

Let's run a container with JupyterLab:
``sudo docker run -p 80:8888 jupyter/base-notebook start-notebook.sh --IdentityProvider.token=''``

Now this container runs on Odroid, but it's also exposed to the local network.
The JupyterLab can be accessed from another computer usind the Odroid's IP address,
just type ``http://[your_odroid_address]`` in your browser:



Finish
~~~~~~~~~~~~~~~~~~~

Now python code or shell commands can be executed on docker container running on Odroid,
but some additional settings will be needed to get access to the camera or motors of a robot.

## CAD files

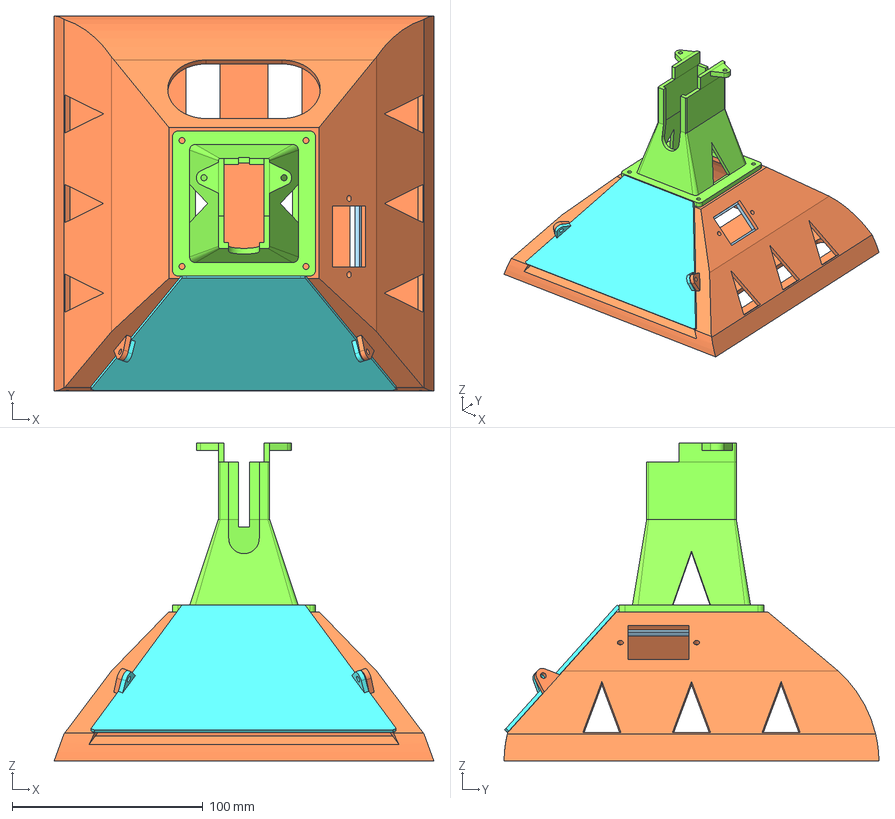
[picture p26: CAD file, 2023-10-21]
3d source/1_Base/1_Base_Assembly.FCStd
199.1 x 196.6 x 166.7 mm
1_Base_Box_001
1_Base_Door_001
1_Base_Stand_001
1_Base_Switch_Body_001

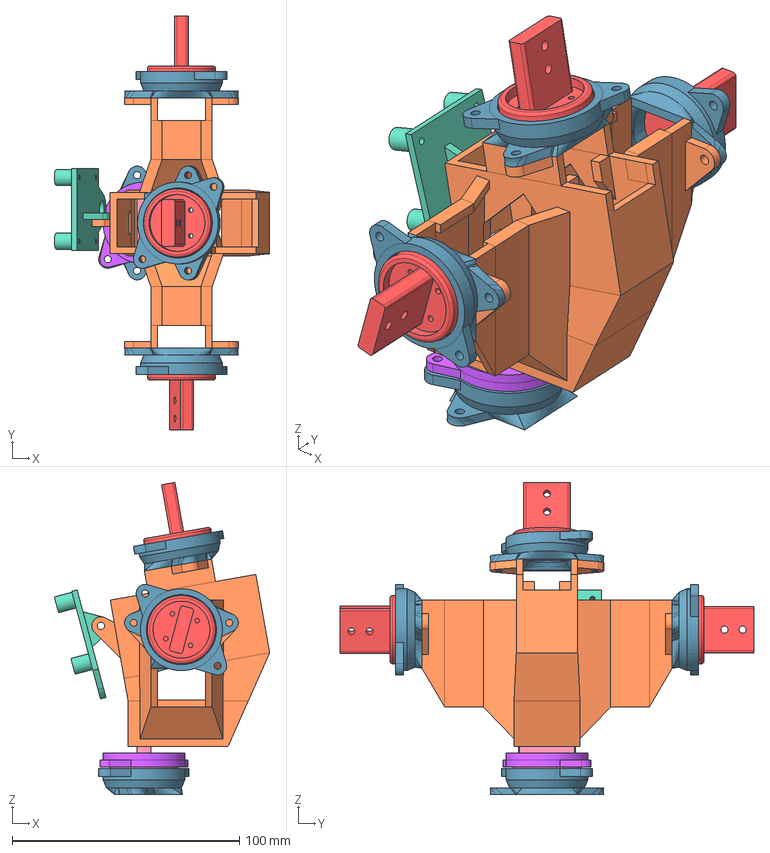
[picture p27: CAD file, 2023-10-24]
3d source/2_Chest/2_Chest_Assembly.FCStd
94.7 x 182.0 x 137.2 mm
2_Chest_Main_001
2_Chest_Camera_Mount_001
2_Chest_Joint_Big_001
2_Chest_Joint_Cap_001
2_Chest_Motor_Cap_001
2_Chest_Joint_Small_001
2_Chest_Motor_Cap_002
2_Chest_Joint_Small_002
2_Chest_Motor_Cap_003
2_Chest_Joint_Small_003
2_Chest_Motor_Cap_004

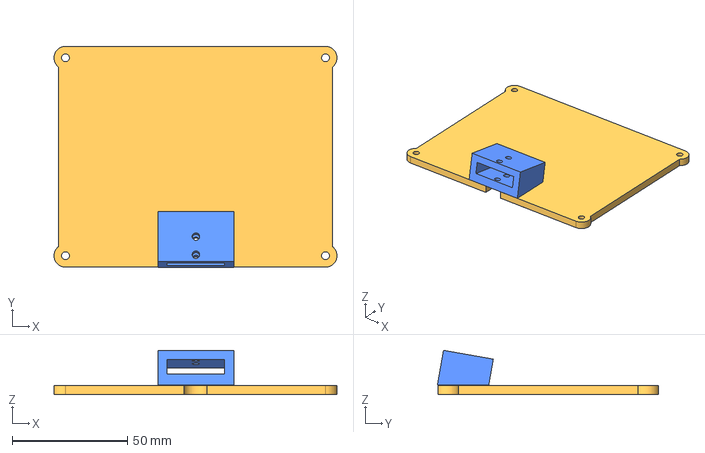
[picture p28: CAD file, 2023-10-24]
3d source/3_Head/3_Head_Assembly.FCStd
123.0 x 96.2 x 19.3 mm
3_Head_Main_001
3_Head_Mount_001

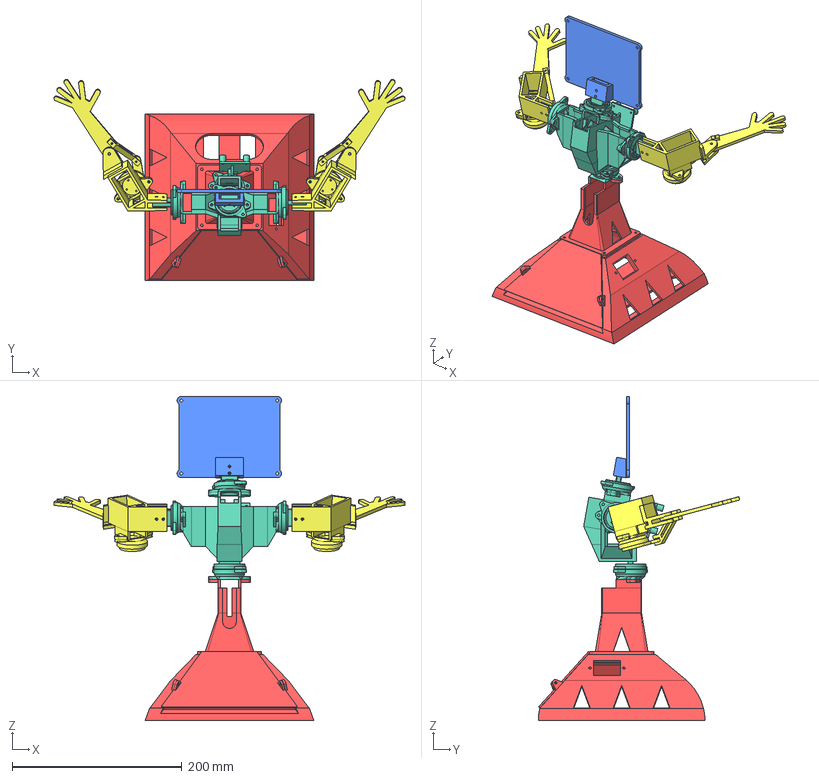
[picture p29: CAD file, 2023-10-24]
3d source/Assembly/Full_Robot.FCStd
413.8 x 237.5 x 382.4 mm
1_Base_Assembly_001
2_Chest_Assembly_001
3_Head_Assembly_001
4_Arms_Assembly_001
4_Arms_Assembly_001 (Mirror #1)

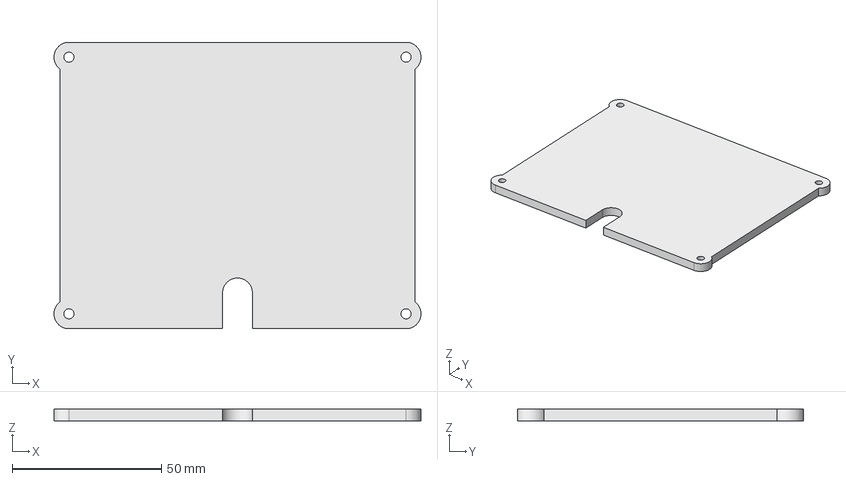
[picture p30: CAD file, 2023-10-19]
3d source/3_Head/3_Head_Main.FCStd
123.0 x 96.0 x 4.00 mm

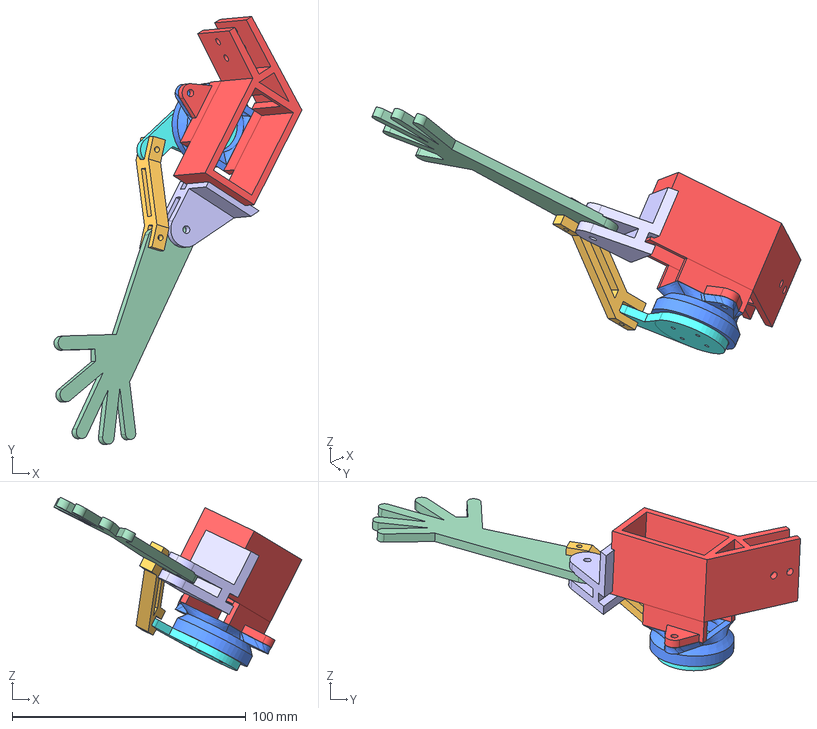
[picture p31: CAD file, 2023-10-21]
3d source/4_Arms/4_Arms_Assembly.FCStd
106.1 x 183.2 x 74.3 mm
4_Arms_Main_L_001
4_Arms_Rod_001
4_Arms_Cap_001
4_Arms_Lever_L_001
4_Arms_Bracket_L_001
4_Arms_Palm_001

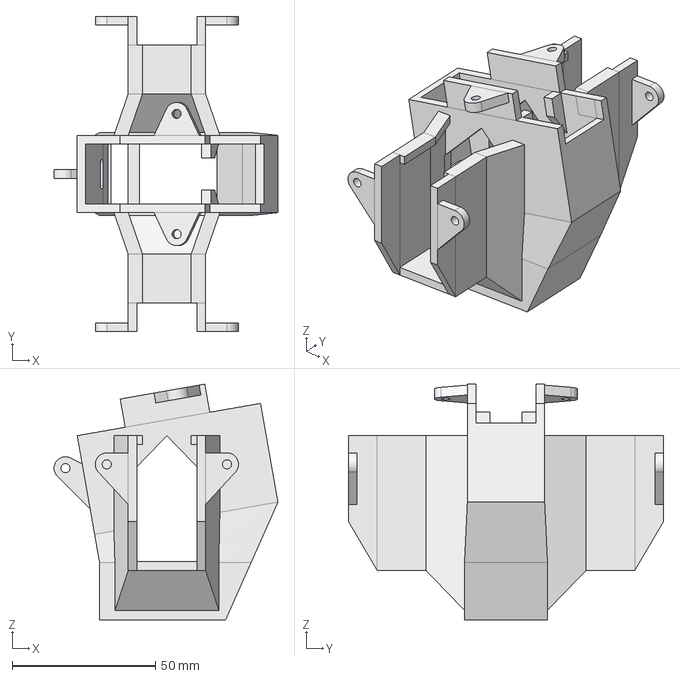
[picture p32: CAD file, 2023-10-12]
3d source/2_Chest/2_Chest_Main.FCStd
78.2 x 110.0 x 82.3 mm

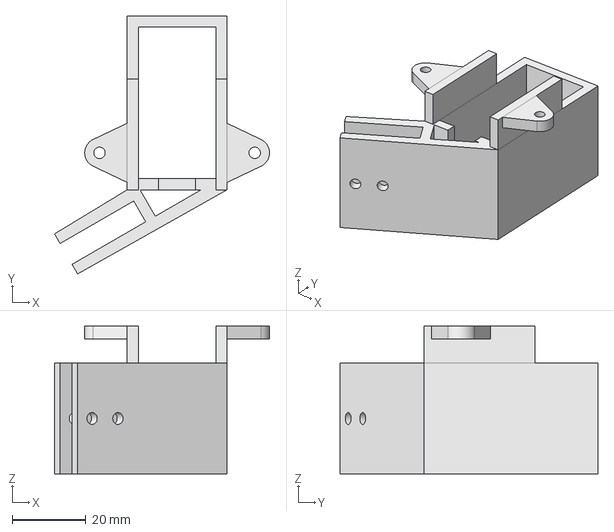
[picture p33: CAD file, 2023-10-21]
3d source/4_Arms/4_Arms_Main_L.FCStd
58.2 x 69.8 x 40.0 mm

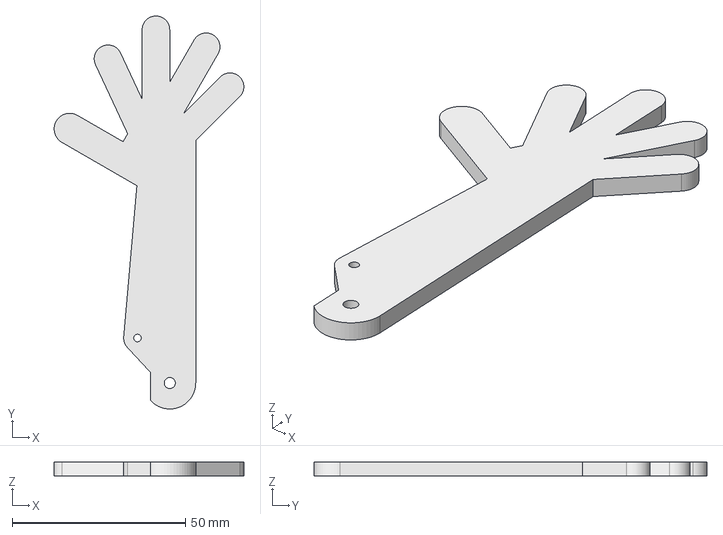
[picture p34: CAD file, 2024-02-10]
3d source/4_Arms/4_Arms_Palm.FCStd
54.8 x 113.5 x 4.00 mm

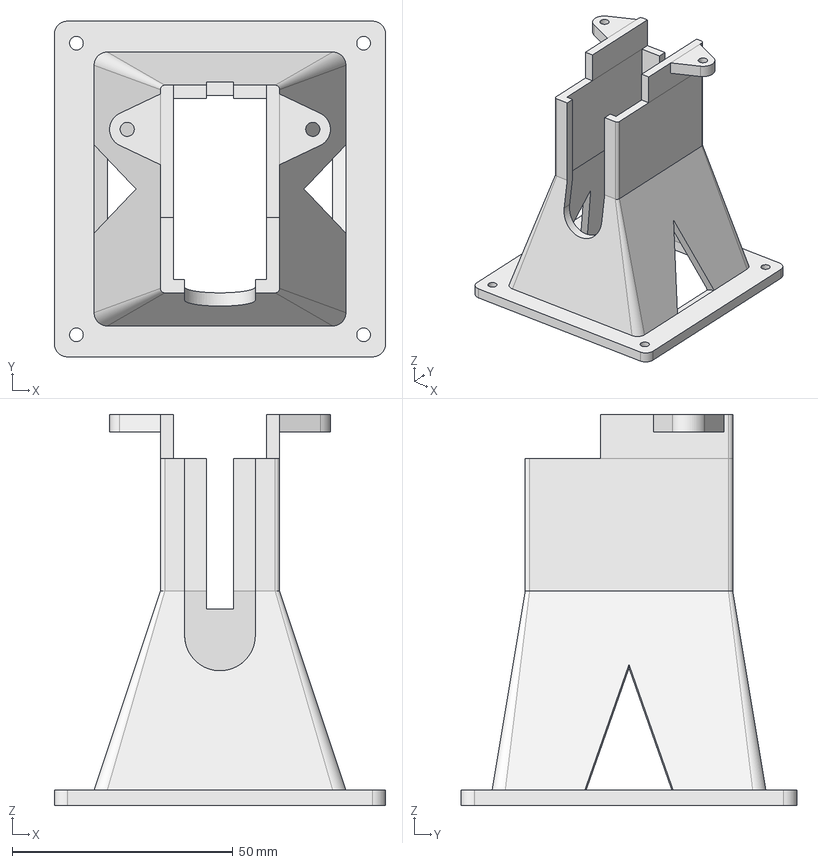
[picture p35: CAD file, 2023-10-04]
3d source/1_Base/1_Base_Stand.FCStd
75.0 x 76.0 x 88.5 mm

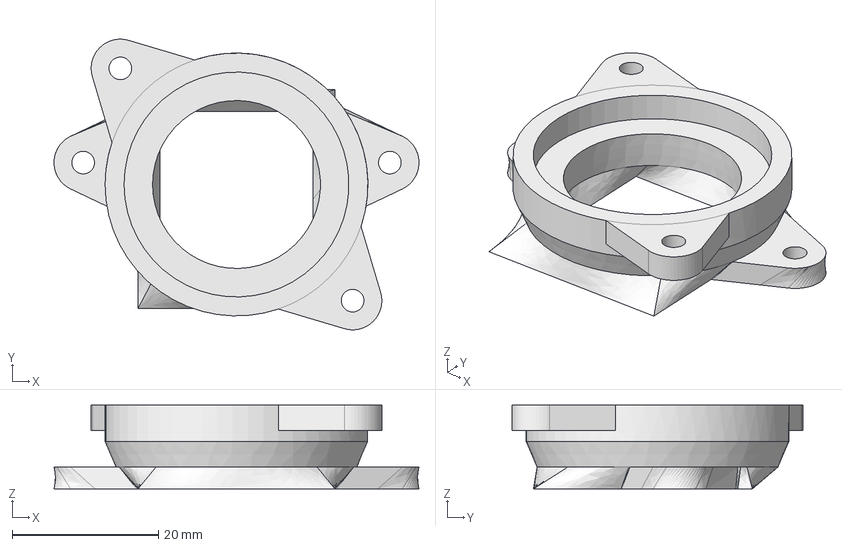
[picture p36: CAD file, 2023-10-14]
3d source/2_Chest/2_Chest_Motor_Cap.FCStd
50.0 x 39.8 x 11.5 mm

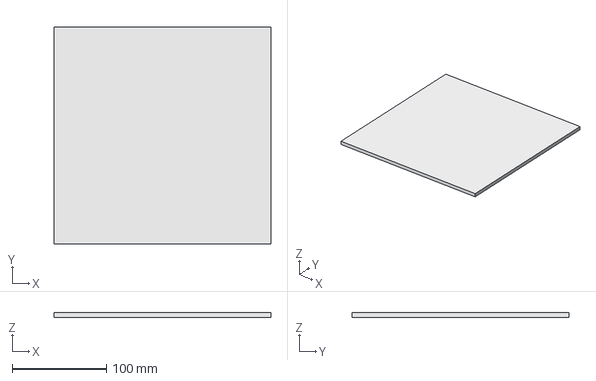
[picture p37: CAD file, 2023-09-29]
3d source/Assembly/Table.FCStd
230.0 x 230.0 x 5.00 mm

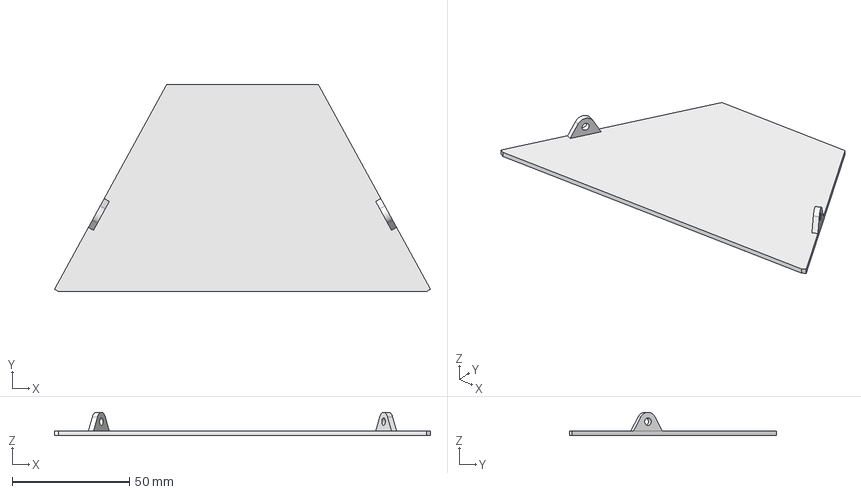
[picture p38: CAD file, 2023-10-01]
3d source/1_Base/1_Base_Door.FCStd
160.1 x 88.1 x 9.99 mm

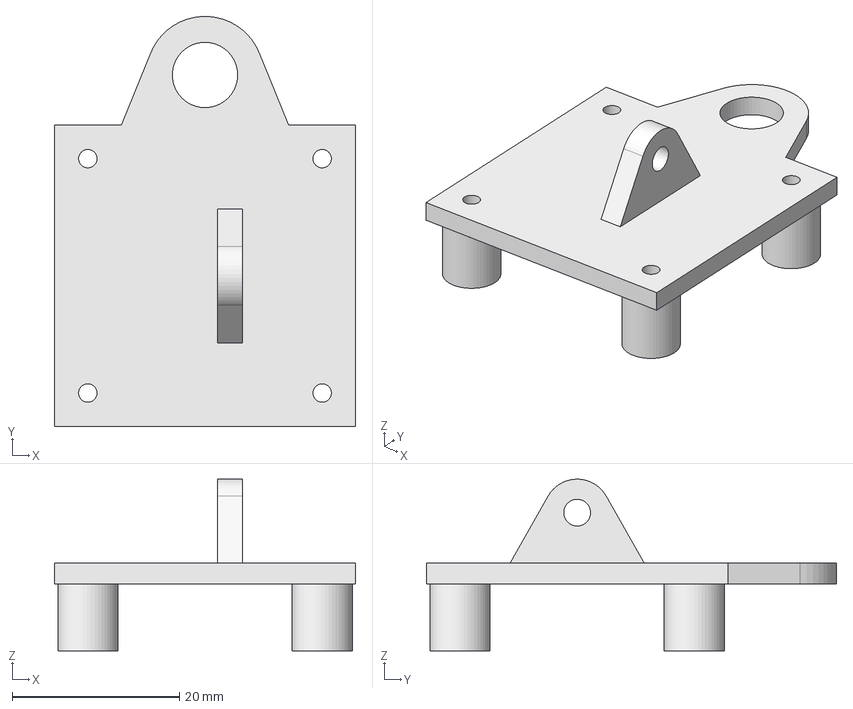
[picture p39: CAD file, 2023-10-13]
3d source/2_Chest/2_Chest_Camera_Mount.FCStd
36.0 x 49.0 x 20.5 mm

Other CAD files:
3d source/4_Arms/4_Arms_Main_R.FCStd
3d source/3_Head/3_Head_Mount.FCStd
3d source/4_Arms/4_Arms_Lever_L.FCStd
3d source/Assembly/Screen.FCStd
3d source/1_Base/1_Base_Box.FCStd
3d source/1_Base/1_Base_Box_Door.f3d
3d source/1_Base/1_Base_Switch.FCStd
3d source/2_Chest/2_Chest_Joint_Big.FCStd
3d source/2_Chest/2_Chest_Joint_Cap.FCStd
3d source/2_Chest/2_Chest_Joint_Small.FCStd
3d source/4_Arms/4_Arms_Bracket_L.FCStd
3d source/4_Arms/4_Arms_Bracket_R.FCStd
3d source/4_Arms/4_Arms_Cap.FCStd
3d source/4_Arms/4_Arms_Lever_R.FCStd
3d source/4_Arms/4_Arms_Rod.FCStd
3d source/Assembly/Arm.FCStd
3d source/Assembly/Bottom.FCStd
3d source/Assembly/Full_Robot.blend
3d source/Assembly/Full_Robot.obj
3d source/Assembly/Full_Robot.stl
STL/1_Base/1_Base_Assembly.stl
STL/1_Base/1_Base_Box.stl
STL/1_Base/1_Base_Door.stl
STL/1_Base/1_Base_Stand.stl
STL/1_Base/1_Base_Switch.stl
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

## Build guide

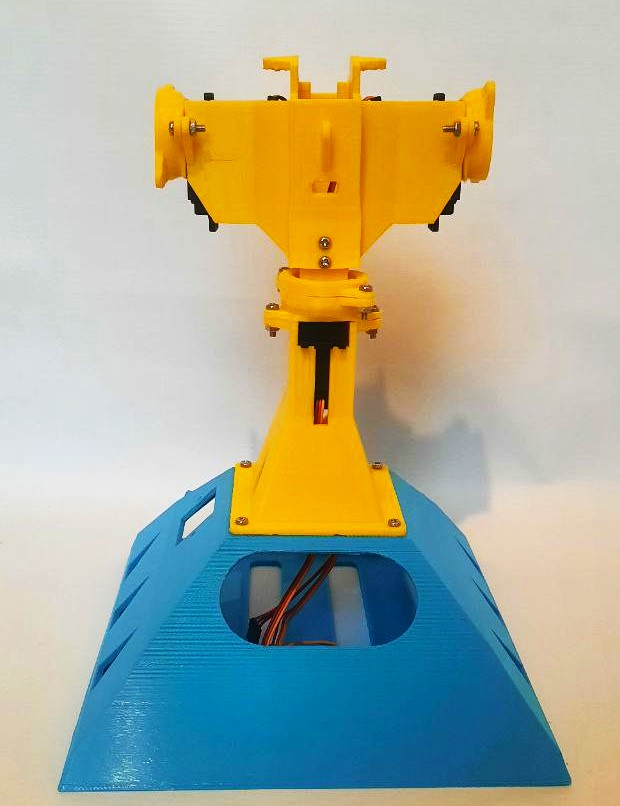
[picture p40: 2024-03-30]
docs/images/Robot assembling/2_Chest_Motor_Cap1.jpg

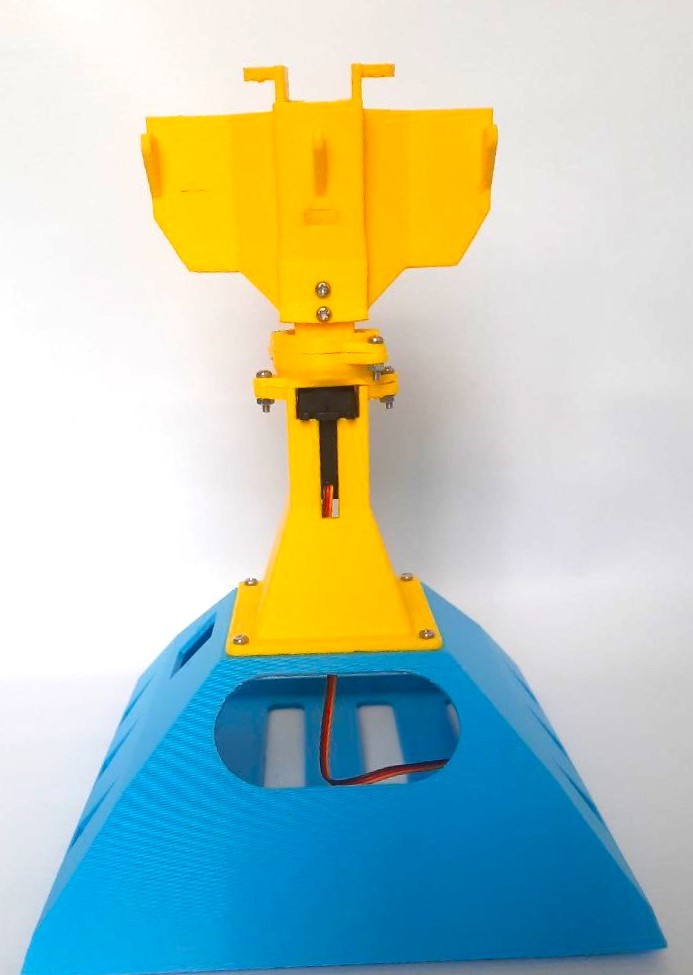
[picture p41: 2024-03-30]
docs/images/Robot assembling/2_Chest_Main.jpg

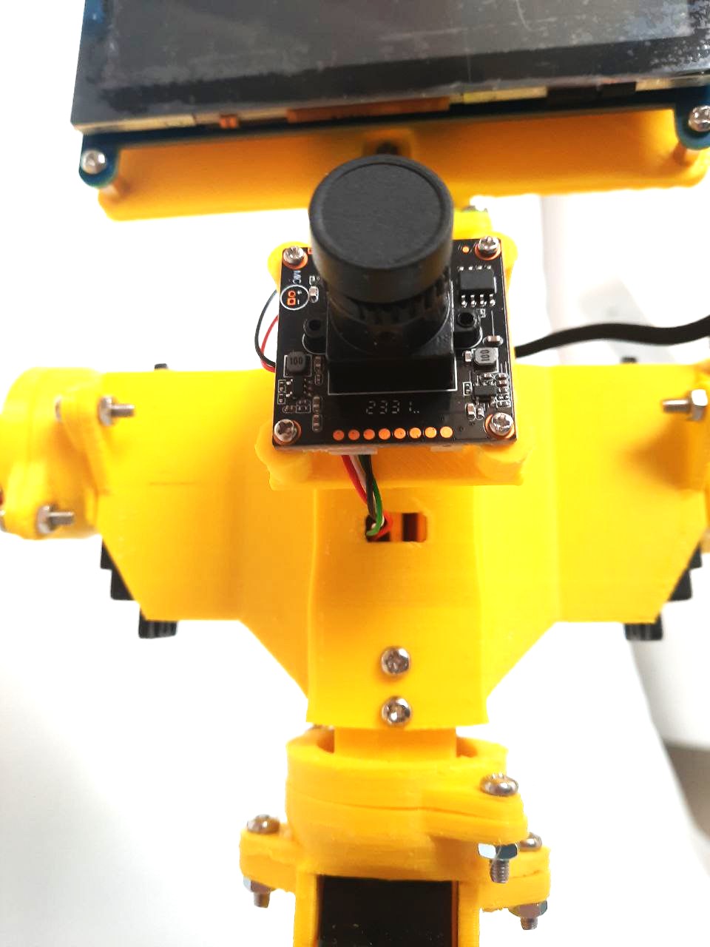
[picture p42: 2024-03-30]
docs/images/Robot assembling/camera.jpg

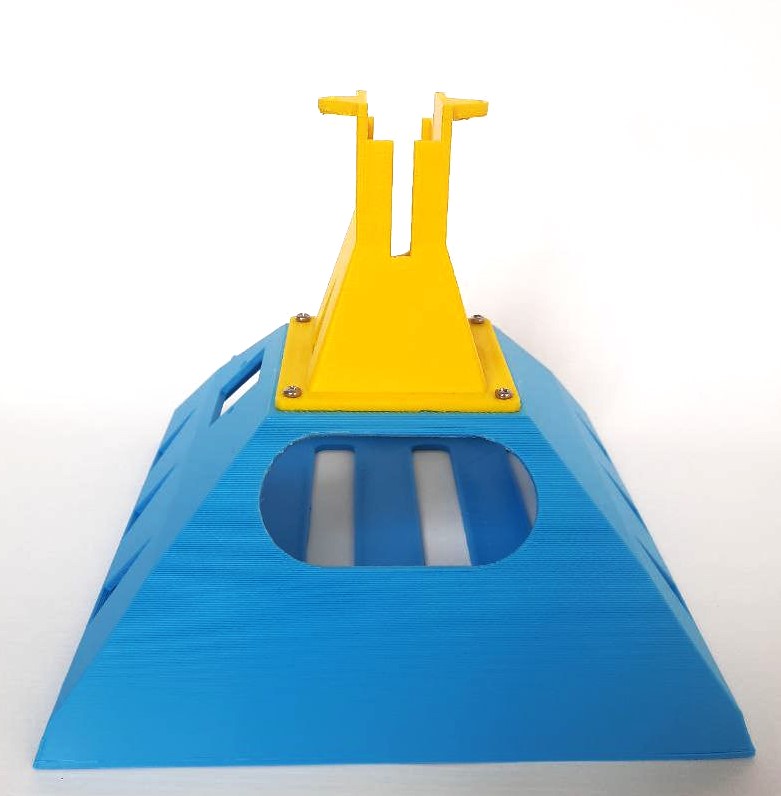
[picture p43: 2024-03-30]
docs/images/Robot assembling/1_Base_BoxStand2.jpg

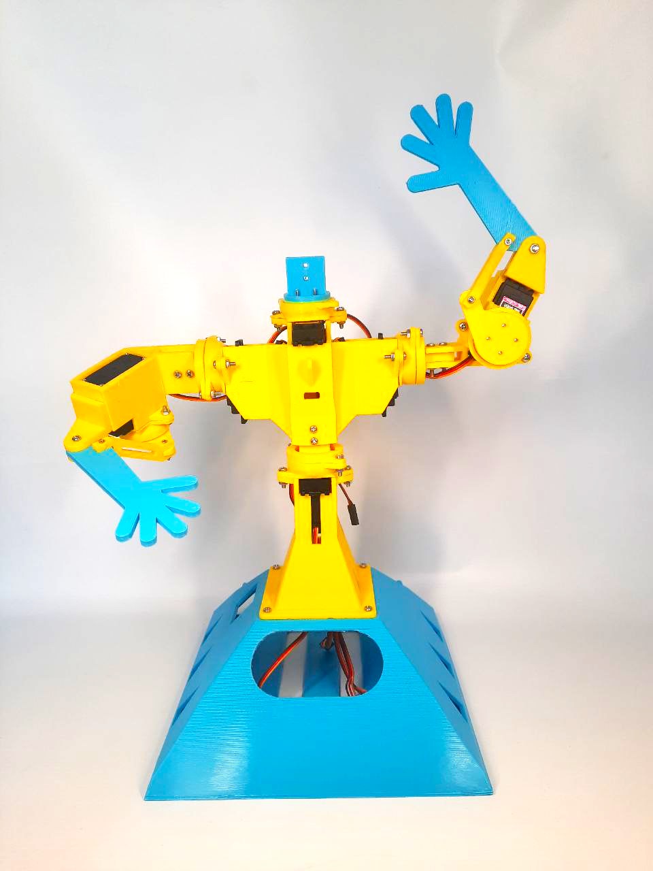
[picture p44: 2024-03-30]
docs/images/Robot assembling/4_Arms_Rod2.jpg

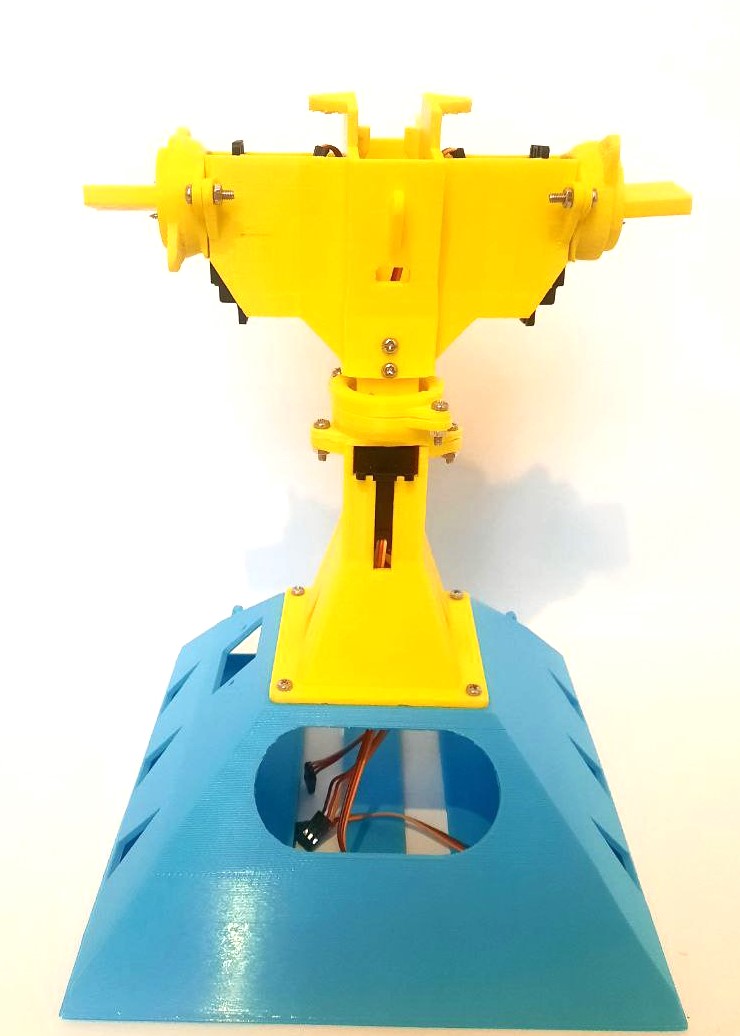
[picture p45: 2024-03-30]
docs/images/Robot assembling/2_Chest_Joint_Cap4.jpg

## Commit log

2023-08-03 3d files (source and STL) added
    [0_Base_Buttom.FCStd, 0_Base_Buttom.stl, 0_Base_CameraMount.FCStd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]
2023-08-05 Added BOM
2023-08-05 docs: added BOM to supply
2023-08-22 base box added
    [0_Base_Box.FCStd, 0_Base_Box.stl]
2023-08-23 Add files via upload
    changed the box
    [0_Base_Box.FCStd]
2023-08-23 Added cover for the box
    [0_Base_Cover.FCStd, 0_Base_Cover.stl]
2023-08-23 divided the box into bottom and top parts
    [0_Base_Box-Body.stl, 0_Base_Box.stl, 0_Base_Box_Bottom.FCStd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]
2023-08-23 Fixed the Curcuit
    [0_Base_Box.FCStd, 0_Base_Box.stl]
2023-08-24 Divided bottom part into two
    [0_Base_Box_Bottom.FCStd, 0_Base_Box_Bottom.stl, 0_Base_Box_Bottom_Left.FCStd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]
2023-08-24 devided base in two more parts
    [0_Base_Box_Bottom_Left.FCStd, 0_Base_Box_Bottom_LeftBack.FCStd, 0_Base_Box_Bottom_LeftBack.stl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]
2023-08-24 divided old parts
    [0_Base_Box_Bottom_Left.stl, 0_Base_Box_Bottom_Right.FCStd, 0_Base_Box_Bottom_Right.stl]
2023-09-04 Electric circuit docs fixes
2023-09-14 docs: camera video example
2023-09-14 docs: camera video fix
2023-09-22 Bottom assembly added
    [0_Base_Box_Bottom_LeftBack.FCStd, 0_Base_Cover.FCStd, Bottom.FCStd]
2023-09-23 Full robot assembly
    [Full_Robot.FCStd]
2023-09-26 Base Box Top - added button and speaker
    [0_Base_Box_Top.FCStd, 0_Base_Box_Top.stl]
2023-09-27 Arm assembly and Full robot finished
    [Arm.FCStd, Full_Robot.FCStd]
2023-09-27 Assemblies with speaker hole
    [Bottom.FCStd, Full_Robot.FCStd]
2023-09-27 bottom stl: increased speaker hole
    [0_Base_Box_Top.FCStd, 0_Base_Box_Top.stl]
2023-09-27 Fixed base box LeftFront and RightFront STL's
    [0_Base_Box_Bottom_LeftFront.stl, 0_Base_Box_Bottom_RightFront.stl, 0_Base_Buttom.FCStd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]
2023-09-28 Base box made in one piece
    [0_Base_Box.FCStd, 0_Base_Box.stl]
2023-09-29 Base box: cooling added
    [0_Base_Box.FCStd, 0_Base_Box.stl]
2023-09-29 Base box: reduced size 200*195
    [0_Base_Box.FCStd, 0_Base_Box.stl]
2023-09-29 Base: reduced number of parts
    [0_Base_Box_Bottom_LeftBack.FCStd, 0_Base_Box_Bottom_LeftBack.stl, 0_Base_Box_Bottom_LeftFront.FCStd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]
2023-09-29 Render added
    [3_Head_Tall.FCStd, Full_Robot.FCStd, Full_Robot.step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]
2023-09-29 docs: 3d printing added
2023-09-29 docs: 3d printing fix
2023-09-29 docs: 3d print images added
2023-09-29 docs: link to github added for 3d printed parts
2023-09-30 stl: stand modified
    [1_Stand_Main.FCStd, 1_Stand_Main.stl]
2023-09-30 full robot render with the face
    [Full_Robot.FCStd, Full_Robot.blend, Full_Robot.obj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]
2023-10-01 stl: base box enlarged
    [0_Base_Box.FCStd, 0_Base_Box.stl]
2023-10-01 stl: stand changed to fit the base
    [0_Base_Box.FCStd, 1_Stand_Main.FCStd, 1_Stand_Main.stl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]
2023-10-01 stl: base door and stand updated
    [0_Base_Door.FCStd, 0_Base_Door.stl, 1_Stand_Main.FCStd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]
2023-10-03 stl: chest made in one piece
    [2_Chest_Main_New.FCStd, 2_Chest_Main_New.stl]
2023-10-04 stl and docs: base stand modified
    [0_Base_Box.FCStd, 0_Base_Box.stl, 0_Base_Door.FCStd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]
2023-10-04 docs: print fix
2023-10-04 stl: new chest_main
    [2_Chest_Main.FCStd, 2_Chest_Main.stl, 2_Chest_Main_1.FCStd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]
2023-10-12 stl: chest fix
    [2_Chest_Main.FCStd, 2_Chest_Main.stl]
2023-10-13 stl: added camera mount
    [2_Chest_Camera_Mount.FCStd, 2_Chest_Camera_Mount.stl]
2023-10-14 stl: chest motor cap edited
    [2_Chest_Motor_Cap.FCStd, 2_Chest_Motor_Cap.stl]
2023-10-17 stl: forearm with fingers
    [5_Forearm_Main.FCStd, 5_Forearm_Main.stl]
2023-10-17 stl: upper arm fixed
    [4_UpperArm_Rod.FCStd, 4_UpperArm_Rod.stl, 5_Forearm_Main.FCStd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]
2023-10-18 docs: updated stl pictures
2023-10-18 stl: obsolete head files removed
    [3_Head_Mount_Tall.FCStd, 3_Head_Mount_Tall.stl, 3_Head_Tall.FCStd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]
2023-10-18 stl: arm improved
    [4_UpperArm_Bracket.FCStd, 4_UpperArm_Bracket.stl, 4_UpperArm_Lever.FCStd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]
2023-10-18 stl: fixes
    [3_Head_Main.FCStd, 4_UpperArm_Lever.stl, 4_UpperArm_Rod.stl]
2023-10-19 stl: head fixed
    [3_Head.stl, 3_Head_Main.FCStd, 3_Head_Main.stl]
2023-10-20 3d printing for readthedocs
    [4_Arms_Bracket.stl, 4_Arms_Cap.stl, 4_Arms_Lever.stl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]
2023-10-20 stl: added assembly stl
    [Full_Robot.stl]
2023-10-21 stl source: files moved
    [4_Arms_Bracket.FCStd, 4_Arms_Cap.FCStd, 4_Arms_Lever.FCStd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]
2023-10-21 stl: arm edited
    [4_Arms_Bracket.FCStd, 4_Arms_Bracket.stl]
2023-10-21 Added parts for left and right hands separately
    [4_Arms_Bracket_L.FCStd, 4_Arms_Bracket_L.stl, 4_Arms_Bracket_R.FCStd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]
2023-10-21 Added printer photo and description
2023-10-21 Assemblies of Valera's zones
    [1_Base_Assembly.FCStd, 1_Base_Assembly.stl, 2_Chest_Assembly.FCStd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]
2023-10-22 docs: 3d print fix
2023-10-24 Full robot 3d model
    [2_Chest_Assembly.FCStd, 3_Head_Assembly.FCStd, Full_Robot.FCStd]
2023-10-24 docs: 3d print edited
2023-10-24 Head assembly photo fixed
2023-10-29 Added an essay about servo motors
2023-10-29 Servo essay fix
2023-10-29 docs: servo - video added
2023-10-29 docs: servo fixed
2023-10-29 docs: servo rewritten
2023-10-29 docs: servo - new images
2024-02-10 3d print: increased mobility for the palm
    [4_Arms_Palm.FCStd, 4_Arms_Palm.stl]
2024-03-30 new photo BOM
2024-03-30 new comment bom
2024-03-31 docs: electric circuit updated for Orange PI
2024-03-31 docs: electric circuit - added order in which motors are connected to the servo driver pins
2024-04-01 docs: motors wiring picture added
2024-04-15 3d: 1_base switched to autodesk fusion
    [1_Base_Box.stl, 1_Base_Box_Door.f3d, 1_Base_Door.stl]
2024-05-23 correct photos motordriver and motors order
2024-05-26 stl: quick fix
    [1_Base_Box.stl]
